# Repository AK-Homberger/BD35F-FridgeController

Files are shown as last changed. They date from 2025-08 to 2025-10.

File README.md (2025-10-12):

# BD35F Fridge Controller
An electronic thermostat for a Danfoss/Secop [BD35F](https://assets.danfoss.com/documents/latest/178661/AI376451289296en-000101.pdf) Compressor with ESP8266 (D1 Mini).

Secomp

The Danfoss/Secop BD35F compressor is a widely used DC powered compressor. I'm using it on my boat to cool the fridge. Unfortunately, the original thermostat was defect. Therfore, I decided to create an electronic alternative that has more features than the standard mechanical one.

## Features:
- Uses ESP8266 (D1 Mini) as processor.
- Dual language support (English/German).
- Easy upload of firmware without Arduino IDE possible.
- Temperature is measured with [DS18B20](https://encrypted-tbn0.gstatic.com/shopping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) sensor.
- Implements a Two-Point with I controller to increase the accuracy.
- Supports variable compressor speeds (2000 - 3500 RPM) to adjust cooling capacity and power consumption.
- Supports Boost function to cool down with more power.
- Supports automatic or manual Defrost routine.
- WLAN support (AP or client mode). Configurable via Wifi Manager.
- Browser interface and MDNS support (http://fridgecontrol.local).
- All parameters are configurable with a browser and stored in flash memory of ESP8266.
- [PCB](https://github.com/AK-Homberger/BD35F-FridgeController/blob/main/BD35F-FridgeController/BD35F-FridgeController-PCB.pdf) layout is available in repository (KiCad) and can be orderd from [Aisler.net](https://aisler.net/p/VBBOGMUR).

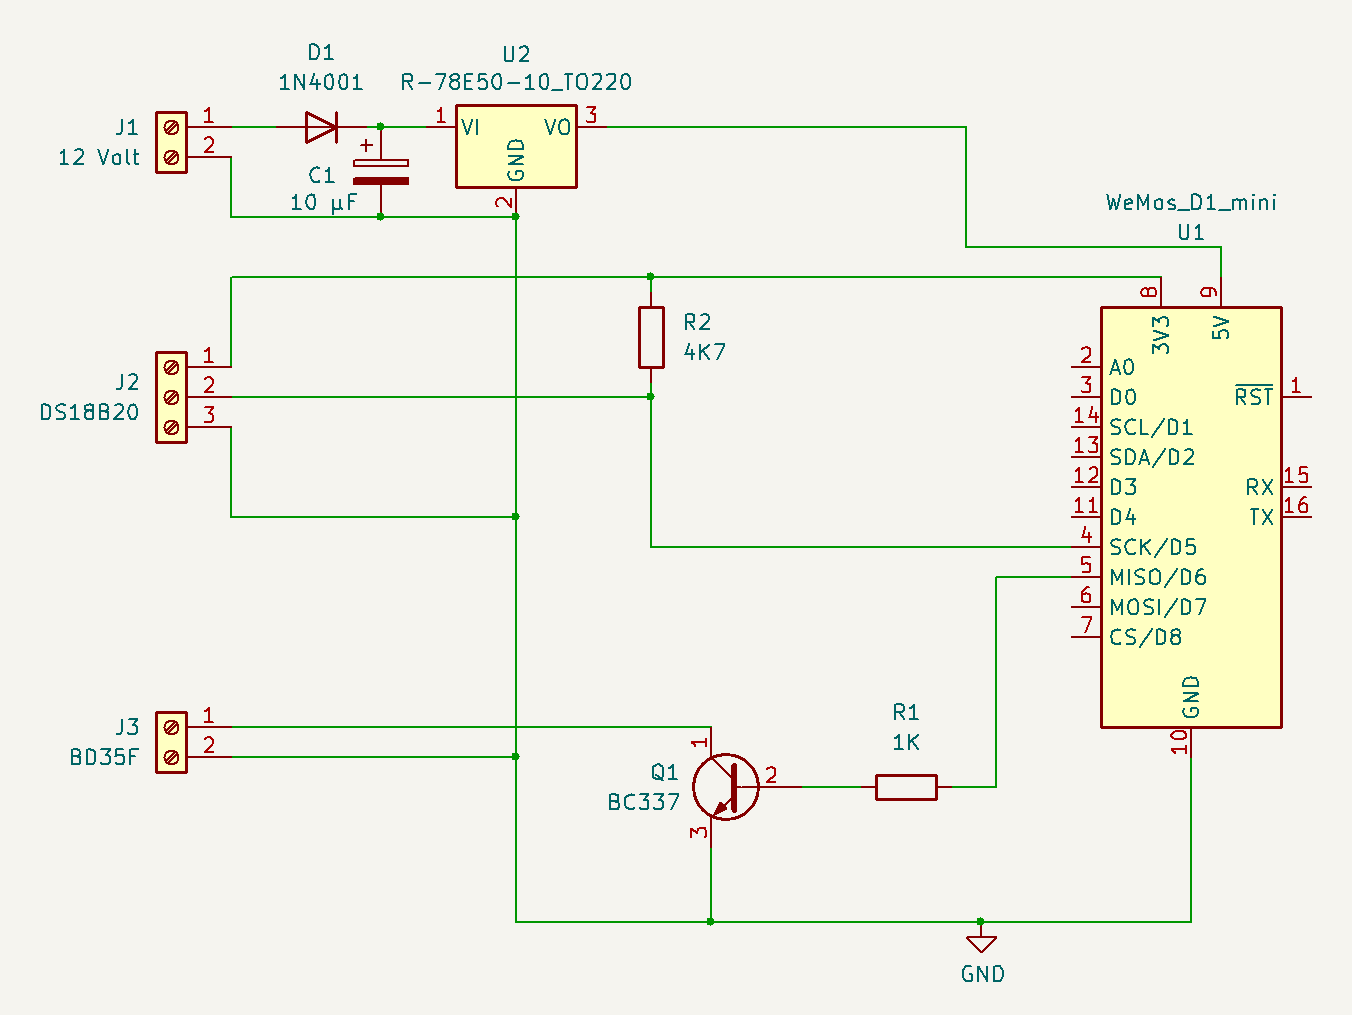
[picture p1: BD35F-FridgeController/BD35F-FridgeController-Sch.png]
Schematic


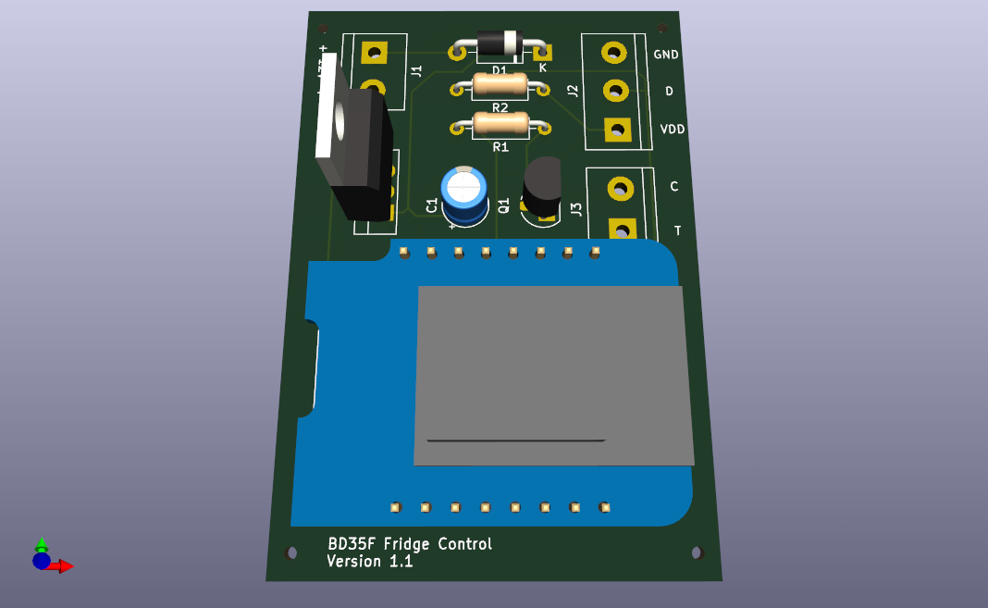
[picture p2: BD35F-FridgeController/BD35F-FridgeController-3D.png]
PCB


## Hardware
The hardware is based on an ESP8266 (D1 Mini) and a few additional parts. The 5 Volt supply voltage for the D1 Mini is created with a [step-down](https://www.reichelt.de/de/de/shop/produkt/dc_dc-wandler_r78e_5_v_500_ma_single-159161) converter. 
The temperature is measuered with a [DS18B20](https://www.analog.com/media/en/technical-documentation/data-sheets/ds18b20.pdf) sensor. The compressor is controlled with an open collector transistor between the connection T and C on the BD35F. 

The BD35F is measuering the current between T and C. C is on GND level and T has a pull-up resistor to 5 Volt. Only a few milliampere are flowing. A small NPN transitor (BC337) is sufficient here. There are two options: T permanently on GND level means 2000 RPM speed. A PWM signal (5 KHz) with a defined duty-cycle is used to set speeds from 2000 to 3500 RPM.

The PCB has three connectors:

### 1. Power 
Connect +/-to 12 Volt to the J1 connector. There is a protection against wrong cabling for +/-.

### 2. DS18B20 Temperature Sensor
Connect the three cables from the DS18B20 to the connector J2. The data line has already the pull-up resistor on the PCB. Red = VDD, Yello = D, Blue = GND.
Place the Sensor in the Fridge in middle highth.

### 3. BD35F Compressor
Connect J3 to the compressor connector. Remove the old thermostat cables and connect the cables C and  T to the compressor. You need appropriate cable shoes for the connection.

## Software
There are two ways to install the software to the D1 Mini. Either you install the Arduino IDE or you direcly flash the BIN-file to the device.

### Arduino IDE
Just [download](https://www.arduino.cc/en/software/) the IDE (version 2.x works well). Then add the Boad URL in preferences: "https://arduino.esp8266.com/stable/package_esp8266com_index.json" and install the Board software in the IDE. Then install the following libraries with the library manager:

- WiFiManager
- ArduinoJson
- OneWire
- DallasTemperature
- Preferences

Then download the sketch from GitHud (Button "Code" and download as ZIP) and extract it. Then move to the [FridgeControl.ino](https://github.com/AK-Homberger/BD35F-FridgeController/blob/main/FridgeControl/FridgeControl.ino) file and open the sketch.
Connect the D1 mini with an USB-Cable to the PC and upload the sketch to the D1 Mini. Later uploads can be done with the OTA function via network.

### NodeMCU-PyFlasher
This works without installation of the IDE. Simply download the [NodeMCU-PyFlasher](https://github.com/nodemcu/nodemcu-firmware/releases) and start it. 

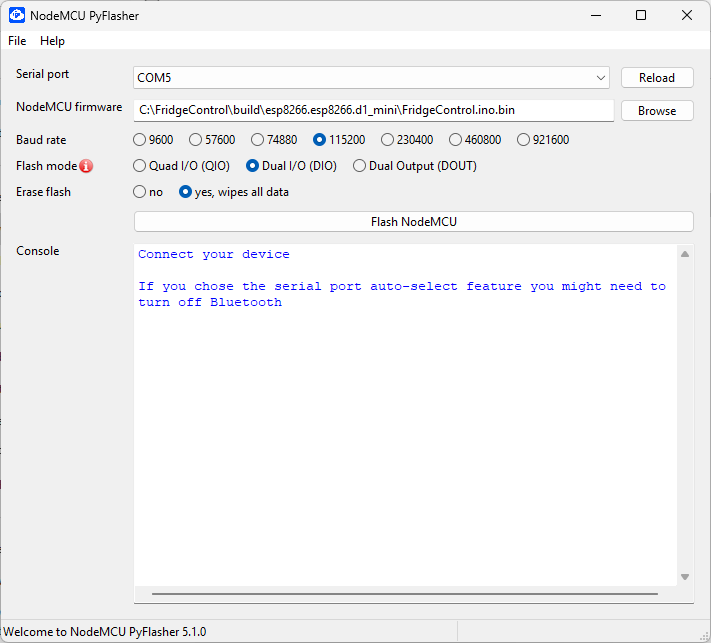
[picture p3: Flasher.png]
Flasher


Select appropriate serial port and then move to the bin file in the deownloaded code. Use the seetings as shown for the upload.

## Usage

After upload of the firmware you have to re-power the device to start the [Wifi-Manager](https://github.com/tzapu/WiFiManager) (within 2 minutes after restart). Just look for a new WLAN network with the name "Fridgeconfig_AP" and connect to it, without a password. The browser will start automatically. Then select the network (ssid) you want to connect to and enter the password. 

If you don't configure or press "Exit" the device remain in AP mode with a changed name "Fridgecontrol_AP".

You can use this to test the device without a real network to connect to. But this is an open connection. Don't use this permanently.

To start the web interface enter "http://fridgecontrol.local" in the browser. The interface looks then like this:

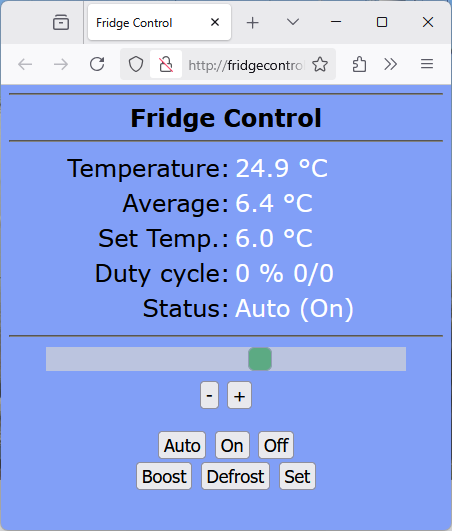
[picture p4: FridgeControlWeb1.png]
Web1


The page shows the current fridge temperature, the average temperature, the desired set temperature. Duty cycle shows the percentage of the on time compared to the last on and off time cycle. The values are also shown in minutes (On/Off). The status filed shows the staus of the controller (Auto, On, Off, Boost or Defrost).

With the slidebar and +/- you can modify the the set temperature.

With the buttons you can set the mode:

- Auto: Standard mode to control the temperature.
- ON: Switch on the compressor permanently.
- Off: Switch off the compressor permanently.
- Boost: Cool down for a defined time with a different set point, hysteresis and speed.
- Defrost: Manually start a defrost cycle.
- Set: Opens a settings page.

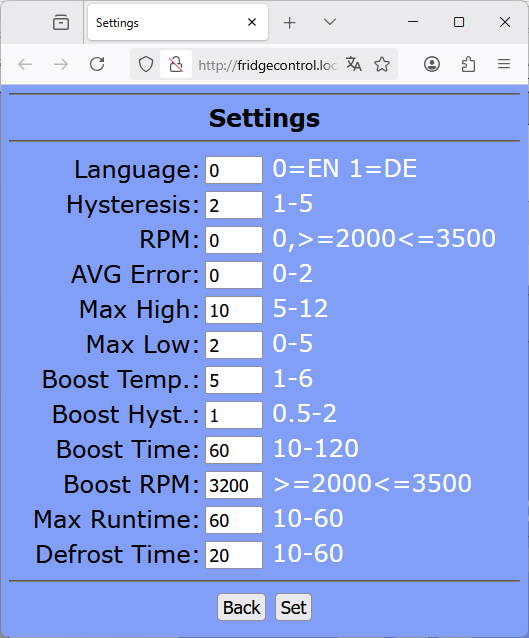
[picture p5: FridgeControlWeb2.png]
Web2


With the settings page you can control the behaviour of the controller without a need to recompile the code. The following settings are available:

- Language:   0=English 1=German language
- Hysteresis: Sets the Hysteresis/deviation for the two point controller. 2 means +/- 2 K. For a set temperature of 6 that means the temperature will between 4 and 8 degrees.
- RPM:         The desired speed of the compressor. Set as low as possible to reduce power consumption (2000 = 3,5A, 3500 = 7A). "0" means T permanently to GND and 2000 RPM (original mechanical thermostat behaviour).
- AVG Error:   This is the allowed deviation from the average. 0 means the compressor will cool down in every cycle until the average temperature reaches the set temperature. The average temperature is calculated with a low pass filter with K of 1/3600. Means average over about one hour.
- Max          High: The maximum high temperture. The compressor will be switched off, if ths level is reached. Independent of average temperature.
- Max Low:     The maximum low temperture. The compressor will be switched on, if ths level is reached. Independent of average temperature.
- Boost Temp.: Desired temperature for the boost function.
- Boost Hyst.: Hysteresis/deviation for the boost function.
- Boost Time   Time in minutes for the boost function.
- Boost RPM:   Compressor speed for the boost function.
- Max Runtime: Used to detect a needed defrost cycle. If the compressor runs for the defined time, a mandatory defrost cycle will start.
- Defrost Time: Set the time for the defrost cycle. Time depends on local fridge details.

After changes press the "Set" butten. The entered value will be checked against the allowed ranges. If everyting is OK you can use "Back" to go back to the main page.

# Parts
- PCB [Aisler](https://aisler.net/p/VBBOGMUR)
- U1 D1 Mini [Link](https://www.reichelt.de/de/en/d1-mini-esp8266-v3-0-d1-mini-p253978.html?&nbc=1)
- U2 Voltage regulator [Link](https://www.reichelt.de/de/de/shop/produkt/dc_dc-wandler_r78e_5_v_500_ma_single-159161)
- R1 Resistor 1 KOhm [Link](https://www.reichelt.de/de/en/carbon-film-resistor-1-4-w-5-1-0-kilo-ohms-1-4w-1-0k-p1315.html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)
- R2 Resistor 4,7 KOhm [Link](https://www.reichelt.com/de/en/shop/product/carbon_film_resistor_1_4_w_5_4_7_kohm-1425)
- Q1 Transistor BC337 [Link](https://www.reichelt.de/de/en/transistor-to-92-bl-npn-45v-800ma-bc-337-25-dio-p219125.html?&nbc=1)
- D1 Diode 1N4001 [Link](https://www.reichelt.de/de/en/rectifier-diode-do41-50-v-1-a-1n-4001-p1723.html?&nbc=1)
- C1 Condensator 10µF [Link](https://www.reichelt.de/de/de/shop/produkt/tantal-kondensator_10_f_10_35v_rm_2_5-20334)
- J1/J3 Connector 2-pin (*2) [Link](https://www.reichelt.de/de/en/2-pin-terminal-strip-spacing-5-08-akl-101-02-p36605.html?&nbc=1)
- J2 Connector 3-pin [Link](https://www.reichelt.com/de/en/shop/product/3-pin_terminal_strip_spacing_5_08-36606)
- DS18B20 [Link](https://www.reichelt.com/de/en/shop/product/shelly_temperature_sensor_ds18b20-287127)

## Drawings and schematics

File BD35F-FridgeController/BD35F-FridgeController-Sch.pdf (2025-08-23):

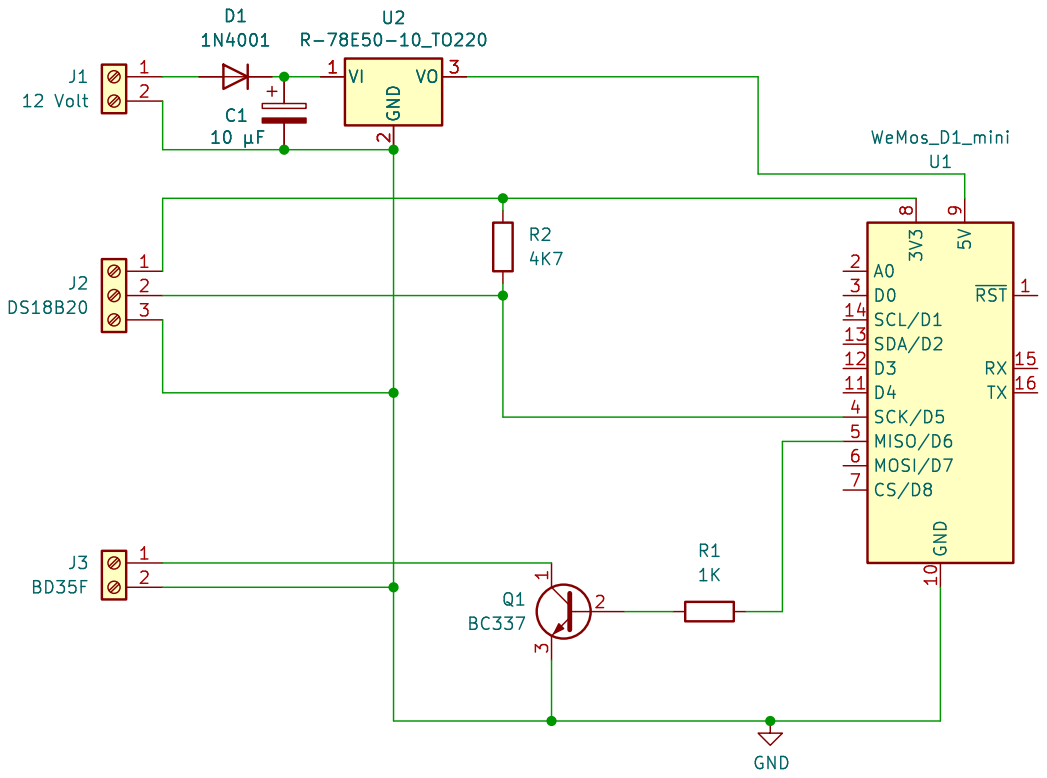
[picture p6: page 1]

2 VO 3 U2 R-78E50-10_TO220 ~{RST}1 GND 10 D4 11 D3 12 SDA/D2 13 SCL/D1 14 RX 15 TX 16 A0 2 D0 3 SCK/D5 4 MISO/D6 5 MOSI/D7 6 CS/D8 7 3V3

Id: 1/1 Title: File: BD35F-FridgeController.kicad_sch Sheet: /

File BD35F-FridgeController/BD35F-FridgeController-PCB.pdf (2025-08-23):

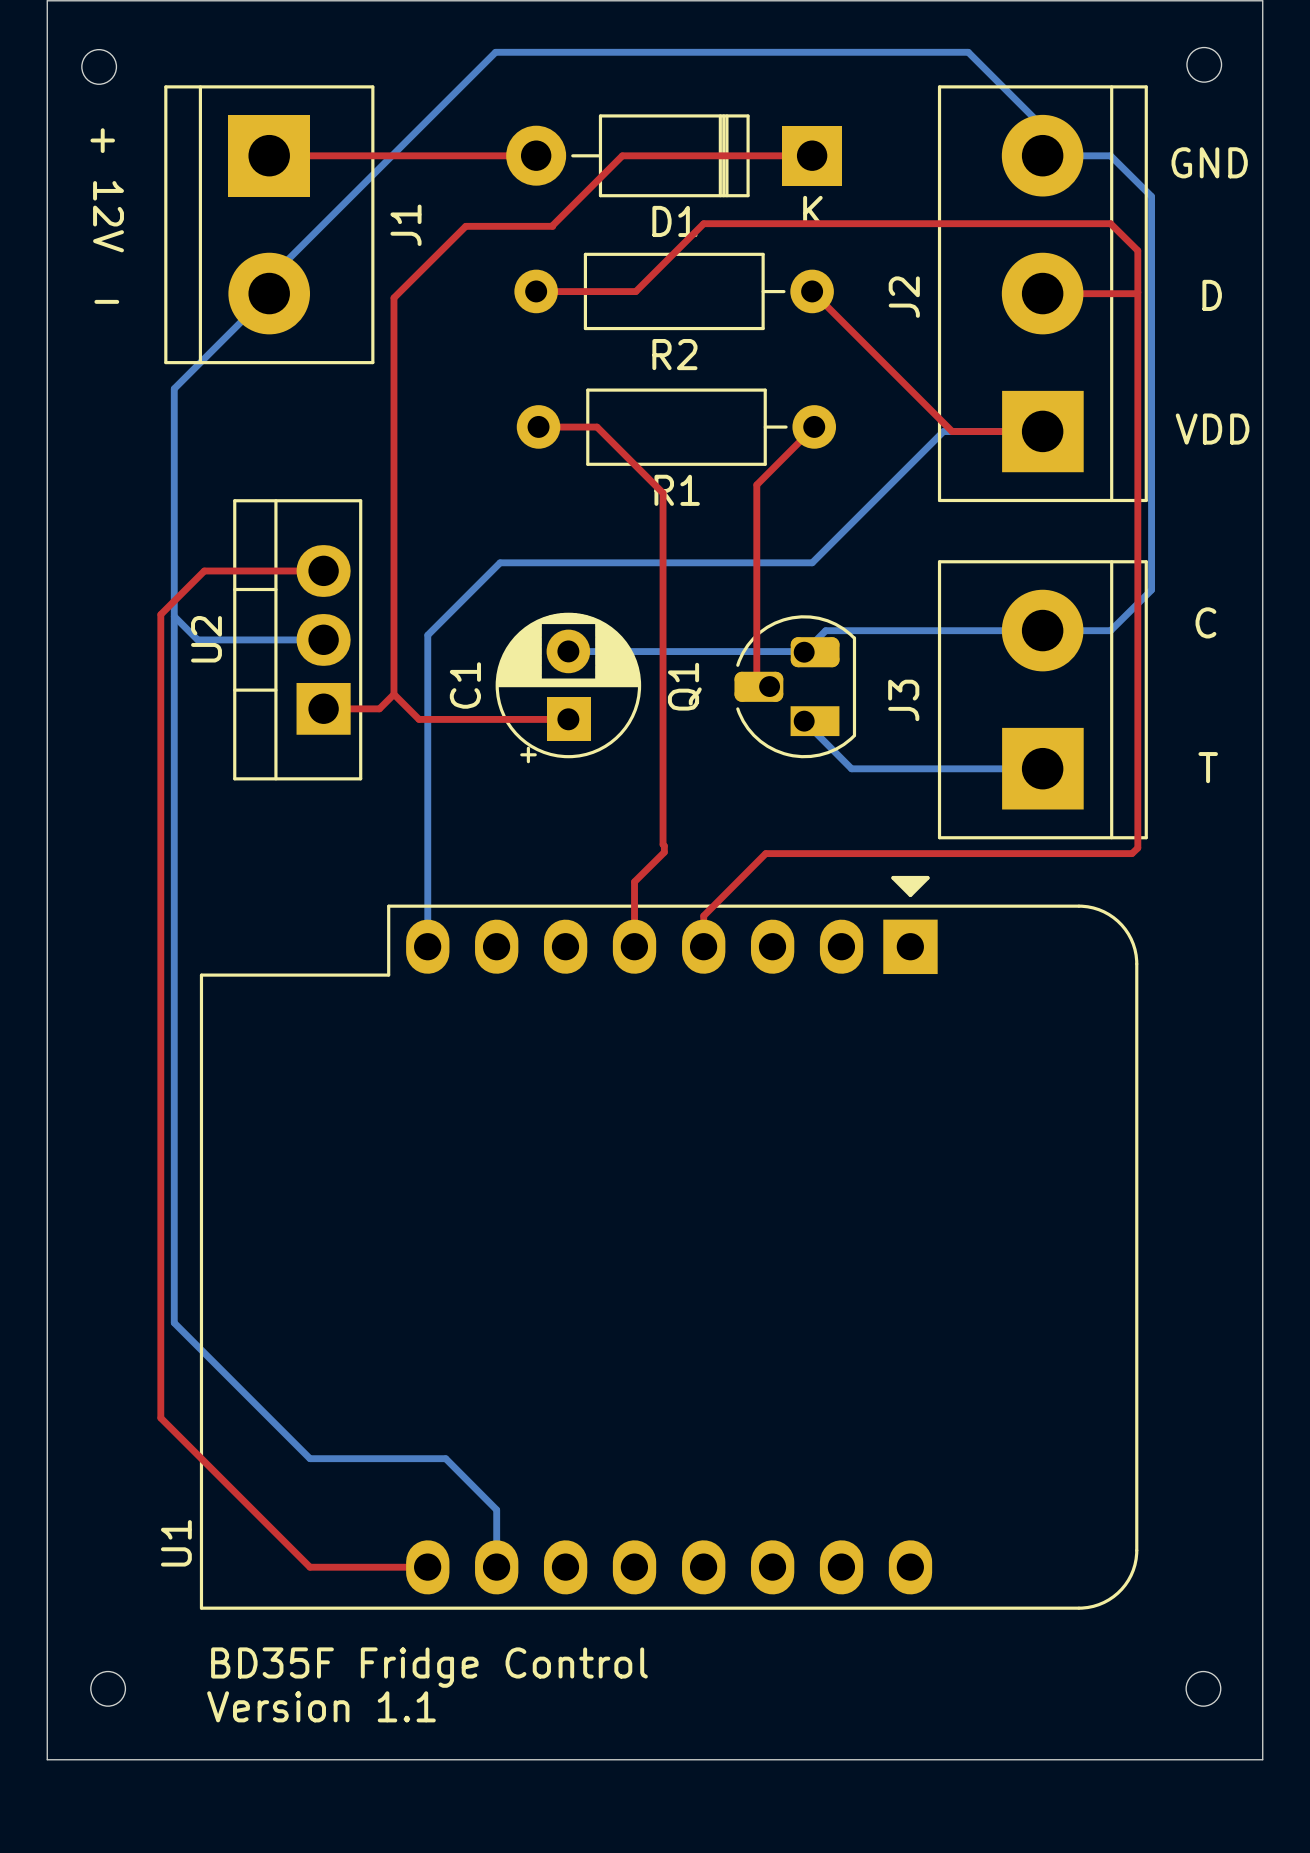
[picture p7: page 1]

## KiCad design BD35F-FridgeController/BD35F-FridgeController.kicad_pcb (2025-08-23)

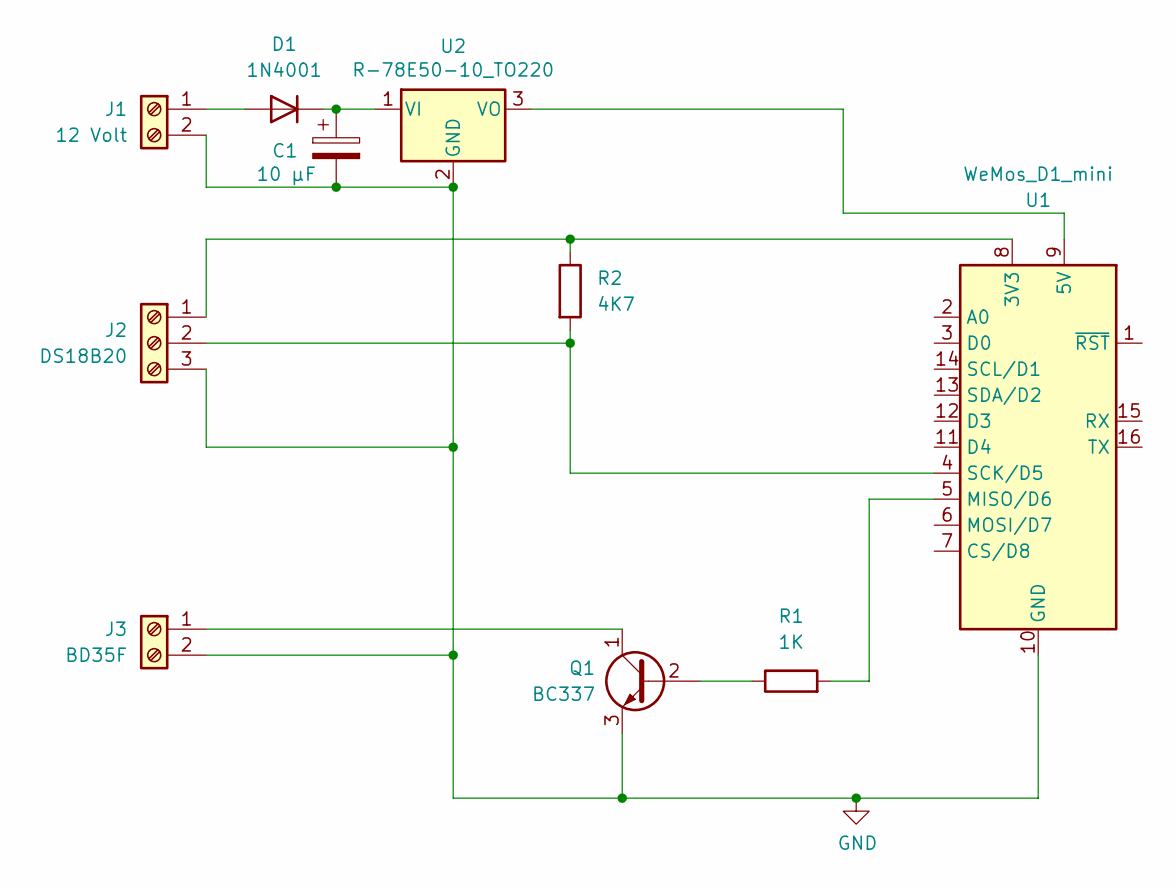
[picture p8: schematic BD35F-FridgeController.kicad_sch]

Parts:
C1: 10 µF; CP_Radial_D5.0mm_P2.50mm
D1: 1N4001; D_DO-41_SOD81_P10.16mm_Horizontal
J1: 12 Volt; TerminalBlock_bornier-2_P5.08mm
J2: DS18B20; TerminalBlock_bornier-3_P5.08mm
J3: BD35F; TerminalBlock_bornier-2_P5.08mm
Q1: BC337; TO-92_HandSolder
R1: 1K; R_Axial_DIN0207_L6.3mm_D2.5mm_P10.16mm_Horizontal
R2: 4K7; R_Axial_DIN0207_L6.3mm_D2.5mm_P10.16mm_Horizontal
U1: WeMos_D1_mini; WEMOS_D1_mini_light
U2: R-78E50-10_TO220; TO-220-3_Vertical

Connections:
GND: C1.2, J1.2, J2.3, J3.2, Q1.3 (E), U1.10 (GND), U2.2 (GND)
unnamed: D1.2 (A), J1.1
unnamed: C1.1, D1.1 (K), U2.1 (VI)
unnamed: J2.1, R2.1, U1.8 (3V3)
unnamed: J2.2, R2.2, U1.4 (SCK/D5)
unnamed: J3.1, Q1.1 (C)
unnamed: Q1.2 (B), R1.1
unnamed: U1.9 (5V), U2.3 (VO)
unnamed: R1.2, U1.5 (MISO/D6)

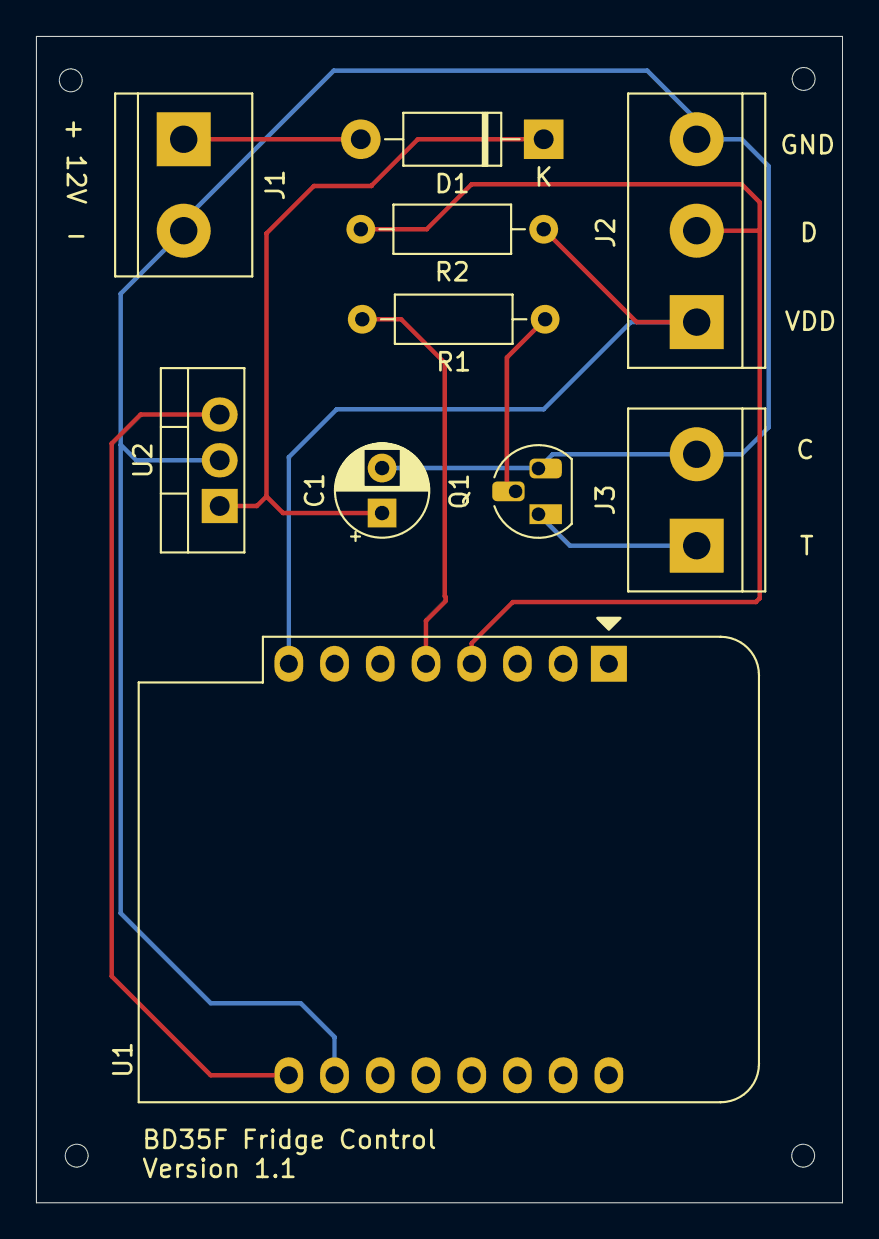
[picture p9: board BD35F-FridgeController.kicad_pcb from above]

Board: 2 copper layers, 44.8 x 64.8 mm, 10 parts (0 on the bottom side), 9 nets.

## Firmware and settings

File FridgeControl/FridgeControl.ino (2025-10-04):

/*
  This code is free software; you can redistribute it and/or
  modify it under the terms of the GNU Lesser General Public
  License as published by the Free Software Foundation; either
  version 2.1 of the License, or (at your option) any later version.
  This code is distributed in the hope that it will be useful,
  but WITHOUT ANY WARRANTY; without even the implied warranty of
  MERCHANTABILITY or FITNESS FOR A PARTICULAR PURPOSE.  See the GNU
  Lesser General Public License for more details.
  You should have received a copy of the GNU Lesser General Public
  License along with this library; if not, write to the Free Software
  Foundation, Inc., 51 Franklin St, Fifth Floor, Boston, MA  02110-1301  USA
*/

// Fridge Control for Danfoss/Secomp BD35F with WLAN and compressor speed setting
// Implements Two-Point with I controller to improve precision of temperature control

// DS18B20 temperature sensor on D5 pin, Relay / PWM output on pin D6
// Use 4k7 Ohm resitor as Pull-Up on D5 (to 3,3 Volt)
// Supports relay output (On/Off) or PWM with NPN transistor to control compressor speed between 2000 and 3500 RPM
// Set PWM to 0 for relay mode
// Connect Relay output (NO) or NPN Transitor (Open Collector) between T and C connection (C = GND, T at 5 Volt level with resistor)
// Current between T and C is only a few mA. A small transistor (eg. BC337) is sufficient. Use 1 kOhm between output pin and basis.

// Version 1.1, 04.10.2025, AK-Homberger
// Corrected duty cycle calculation (double type)

#include <ESP8266WiFi.h>
#include <ESP8266WebServer.h>
#include <ArduinoOTA.h>

// External libraries. Install via Library Manager in IDE
#include <WiFiManager.h>    // https://github.com/tzapu/WiFiManager
#include <ArduinoJson.h>
#include <OneWire.h>
#include <DallasTemperature.h>
#include <Preferences.h>

// Local include
#include "fridge_html_de.h"  // HTML and Javascript code German
#include "fridge_html_en.h"  // HTML and Javascript code English

#define On true
#define Off false

// GPIOs
const int SensorPin = D5;  // DS1820 Sensor
const int FridgePin = D6;  // Relay pin or PWM pin with NPN Transistor

// Put IP address details here
IPAddress AP_local_ip(192, 168, 4, 1);  // Static address for AP
IPAddress AP_gateway(192, 168, 4, 1);
IPAddress AP_subnet(255, 255, 255, 0);

// Fridge
unsigned Language = 0;                  // Language 0=English 1=German
unsigned CurrentRPM = 0;                // Initial RPM. Current value is stored in NVS. 0 = Relay mode
double FridgeTemp = -100;               // Measured fridge temperature
double FridgeTempAvg = -100;            // Average temperature over about one hour (low pass filter)
double FridgeTempLevel = 6;             // Initial temperature level. Current value is stored in NVS
double FridgeHyst = 2;                  // Hysteresis / 2. Max deviation from set temperaure level
double FridgeMaxHigh = 10;              // Maximum temperature. Compressor will switch on above this temperature
double FridgeMaxLow = 2;                // Minimum temperature. Compressor will switch off below this temperature
double FridgeAvgError = 0.1;            // Maximum allowed deviation from average temperatur (forms I part of the control)
bool FridgeAuto = true;                 // Fridge in automatic mode
bool FridgeBoost = false;               // Fridge in boost mode
bool FridgeDefrost = false;             // Fridge in defrost mode
unsigned FridgeDefrostTime = 20;        // Defrost time
unsigned FridgeCurrentDefrostTime = 0;  // Current defrost time
unsigned FridgeMaxRuntime = 60;         // Maximum runtime for compresser. Then defrost
unsigned FridgeCurrentBoostTime = 0;    // Current boost time (counts up to boost time)
double FridgeBoostTemp = 5;             // Fridge boost temperatur (with fixed hysteresis/deviation of 1 K)
double FridgeBoostHyst = 1;             // Set hsyteresis for boost
unsigned FridgeBoostTime = 60;          // Set boost time
unsigned FridgeBoostRPM = 3000;         // Set boost speed for compressor
unsigned FridgeOnTime = 0;              // Current on time of compressor. Counts up.
unsigned FridgeOffTime = 0;             // Current off time of compressor. Counts up.
unsigned FridgeLastOnTime = 0;          // Last on time of compressor to calculate duty cycle
unsigned FridgeLastOffTime = 0;         // Last off time of compressor to calculate duty cycle
bool FridgeOnOff = Off;                 // Current compessor state
bool f_update = false;                  // NVS values changed. Store new values.

// Web Server
ESP8266WebServer web_server(80);  // Web Server at port 80

// Setup a oneWire instance to communicate with any OneWire devices (not just Maxim/Dallas temperature ICs)
OneWire oneWire(SensorPin);
// Pass our oneWire reference to Dallas Temperature.
DallasTemperature sensors(&oneWire);

// Nonvolatile storage on ESP
Preferences preferences;

//*****************************************************************************
void setup() {
  // Sensor and Thermostat pin
  //pinMode(SensorPin, INPUT_PULLUP);  // Comment out if you use an external pull up resistor
  pinMode(FridgePin, OUTPUT);        // Sets relay/PWM pin as output
  analogWriteFreq(5000);             // BD35F expects 5 kHz for PWM with duty cycle control

  // Init serial
  Serial.begin(115200);
  Serial.println();

  WiFiManager wm;
  wm.setConfigPortalTimeout(120);
  
  // Set HTTP request events
  web_server.on("/", HandleRoot);                       // This is the Main display page
  web_server.on("/f_temp", GetFridgeData);              // To get fridge temperature and states
  web_server.on("/f_up", FridgeUp);                     // Fridge + 0.1
  web_server.on("/f_down", FridgeDown);                 // Fridge - 0.1
  web_server.on("/f_auto", Fridge_Auto);                // Fridge Auto state
  web_server.on("/f_boost", Fridge_Boost);              // Fridge Boost state
  web_server.on("/f_defrost", Fridge_Defrost);          // Fridge Defrost state
  web_server.on("/f_on", FridgeOn);                     // Switch fridge On
  web_server.on("/f_off", FridgeOff);                   // Switch fridge Off
  web_server.on("/f_slider", FridgeSlider);             // Handle fridge slider move
  web_server.on("/f_settings", handleSettings);         // Settings page
  web_server.on("/f_get_settings", handleGetSettings);  // JS get settings
  web_server.on("/f_set_settings", handleSetSettings);  // JS save settings

  web_server.onNotFound(HandleNotFound);

  if (!wm.autoConnect("Fridgeconfig_AP")) {
    Serial.println("Start AP");
    WiFi.mode(WIFI_OFF);
    delay(100);
    WiFi.mode(WIFI_AP);
    WiFi.softAP("Fridgecontrol_AP");
    IPAddress IP = WiFi.softAPIP();
    Serial.print("AP IP address: ");
    Serial.println(IP);    
  }

  // Start OneWire
  sensors.begin();
  sensors.setWaitForConversion(false);  // Set to asynchronus mode
  sensors.requestTemperatures();        // Initial request right now

  // Start web server
  web_server.begin();
  Serial.println("HTTP Server started");

  // Start OTA
  ArduinoOTA.setHostname("FridgeControl");  // Arduino OTA config and start
  ArduinoOTA.begin(true);                   // With MDNS (open with http://fridgecontrol.local)

  // Read stored data
  preferences.begin("nvs", false);  // Open nonvolatile storage (nvs)
  Language = preferences.getInt("Language", 0);
  FridgeTempLevel = preferences.getFloat("FridgeTempLevel", 6);
  FridgeHyst = preferences.getFloat("FridgeHyst", 2);
  FridgeMaxHigh = preferences.getFloat("FridgeMaxHigh", 10);
  FridgeMaxLow = preferences.getFloat("FridgeMaxLow", 2);
  FridgeAvgError = preferences.getFloat("FridgeAvgError", 0);
  CurrentRPM = preferences.getInt("RPM", 0);
  FridgeBoostTime = preferences.getInt("FridgeBoostTime", 60);
  FridgeBoostTemp = preferences.getFloat("FridgeBoostTemp", 5);
  FridgeBoostHyst = preferences.getFloat("FridgeBoostHyst", 1);
  FridgeBoostRPM = preferences.getInt("FridgeBoostRPM", 3200);
  FridgeMaxRuntime = preferences.getInt("FridgeMaxRuntime", 60);
  FridgeDefrostTime = preferences.getInt("FridgeDefrostTime", 20);
  preferences.end();
}


//****************************************************************************************
// Read DS1820 sensor once per second (non blocking mode)

void GetTemperature() {
  static float FTO = 0;
  static unsigned long LastTime = 0;
  double tmp = 0;

  if (millis() - LastTime > 1000) {
    tmp = sensors.getTempCByIndex(0);
    //Serial.println(tmp);
    if (tmp != -127) {
      if (abs(FTO - tmp) < 1) FridgeTemp = tmp;
      FTO = tmp;
    }
    LastTime = millis();
    sensors.requestTemperatures();  // Send the command to get temperatures
  }
}


//****************************************************************************************
void HandleRoot() {
  if (Language == 0) web_server.send(200, "text/html", FRIDGE_page_en);  //Send web page
  if (Language == 1) web_server.send(200, "text/html", FRIDGE_page_de);  //Send web page
}


//****************************************************************************************
void handleSettings() {
  if (Language == 0) web_server.send(200, "text/html", Settings_page_en);  //Send settings web page
  if (Language == 1) web_server.send(200, "text/html", Settings_page_de);  //Send settings web page
}


//****************************************************************************************
void handleGetSettings() {
  String Text;
  JsonDocument root;

  root["hyst"] = FridgeHyst;
  root["level"] = FridgeTempLevel;
  root["rpm"] = CurrentRPM;
  root["avgerror"] = FridgeAvgError;
  root["maxhigh"] = FridgeMaxHigh;
  root["maxlow"] = FridgeMaxLow;
  root["boosttime"] = FridgeBoostTime;
  root["boosttemp"] = FridgeBoostTemp;
  root["boosthyst"] = FridgeBoostHyst;
  root["boostrpm"] = FridgeBoostRPM;
  root["maxruntime"] = FridgeMaxRuntime;
  root["defrosttime"] = FridgeDefrostTime;
  root["language"] = Language;

  serializeJsonPretty(root, Text);
  web_server.send(200, "text/plain", Text);  //Send values to client ajax request
}


//****************************************************************************************
void handleSetSettings() {
  float tmp;

  if (web_server.args() == 12) {

    tmp = web_server.arg(0).toFloat();
    if (tmp >= 1 && tmp <= 5) FridgeHyst = tmp;

    tmp = web_server.arg(1).toInt();
    if ((tmp == 0) || (tmp >= 2000 && tmp <= 3500)) CurrentRPM = tmp;  // 0 = Relay mode

    tmp = web_server.arg(2).toFloat();
    if (tmp >= 0 && tmp <= 2) FridgeAvgError = tmp;

    tmp = web_server.arg(3).toFloat();
    if (tmp >= 0 && tmp <= 5) FridgeMaxLow = tmp;

    tmp = web_server.arg(4).toFloat();
    if (tmp >= 5 && tmp <= 12) FridgeMaxHigh = tmp;

    tmp = web_server.arg(5).toInt();
    if (tmp >= 10 && tmp <= 120) FridgeBoostTime = tmp;

    tmp = web_server.arg(6).toInt();
    if (tmp >= 2000 && tmp <= 3500) FridgeBoostRPM = tmp;

    tmp = web_server.arg(7).toFloat();
    if (tmp >= 1 && tmp <= 6) FridgeBoostTemp = tmp;

    tmp = web_server.arg(8).toInt();
    if (tmp >= 10 && tmp <= 60) FridgeMaxRuntime = tmp;

    tmp = web_server.arg(9).toInt();
    if (tmp >= 10 && tmp <= 60) FridgeDefrostTime = tmp;

    tmp = web_server.arg(10).toFloat();
    if (tmp >= 0.5 && tmp <= 2) FridgeBoostHyst = tmp;

    tmp = web_server.arg(11).toInt();
    if (tmp >= 0 && tmp <= 1) Language = tmp;

    web_server.send(200, "text/html");
    f_update = true;
  }
}


//****************************************************************************************
// Handle UP button

void FridgeUp() {
  FridgeTempLevel += 0.1;
  if (FridgeTempLevel > 10) FridgeTempLevel = 10;
  f_update = true;
  web_server.send(200);
}


//****************************************************************************************
// Handle Down button

void FridgeDown() {
  FridgeTempLevel -= 0.1;
  if (FridgeTempLevel < 0) FridgeTempLevel = 0;
  f_update = true;
  web_server.send(200);
}


//****************************************************************************************
// Handle Auto button

void Fridge_Auto() {
  FridgeAuto = true;
  FridgeBoost = false;
  FridgeDefrost = false;
  web_server.send(200);
}


//****************************************************************************************
// Handle Boost button

void Fridge_Boost() {

  FridgeBoost = true;
  FridgeAuto = false;
  FridgeDefrost = false;
  FridgeCurrentBoostTime = 0;

  if (FridgeOnOff == On) {
    FridgeSwitch(Off);
    delay(500);
    FridgeSwitch(On);
  }
  web_server.send(200);
}


//****************************************************************************************
// Handle Defrost button

void Fridge_Defrost() {

  FridgeDefrost = true;
  FridgeAuto = false;
  FridgeBoost = false;
  FridgeCurrentDefrostTime = 0;
  FridgeSwitch(Off);
  web_server.send(200);
}


//****************************************************************************************
// Handle On button

void FridgeOn() {
  FridgeSwitch(On);
  FridgeAuto = false;
  FridgeBoost = false;
  FridgeDefrost = false;
  web_server.send(200);
}


//****************************************************************************************
// Handle Off button

void FridgeOff() {
  FridgeSwitch(Off);
  FridgeAuto = false;
  FridgeBoost = false;
  FridgeDefrost = false;
  web_server.send(200);
}


//****************************************************************************************
// Handle slider event

void FridgeSlider() {
  if (web_server.args() > 0) {
    FridgeTempLevel = web_server.arg(0).toFloat();
  }
  f_update = true;
  web_server.send(200);
}


//****************************************************************************************
// Send temperature, level and status as JSON string

void GetFridgeData() {
  String Text, State;
  char buf[30];
  double dutyCycle = 0;
  JsonDocument root;

  if (FridgeDefrost == true) {
    snprintf(buf, sizeof(buf), "Defrost (%d)", FridgeDefrostTime - (FridgeCurrentDefrostTime / 60));
    State = buf;
  } else if (FridgeBoost == true) {
    if (FridgeOnOff == On) {
      snprintf(buf, sizeof(buf), "Boost (%d)", FridgeBoostTime - (FridgeCurrentBoostTime / 60));
      State = buf;
    }
    if (FridgeOnOff == Off) {
      snprintf(buf, sizeof(buf), "Boost (%d)", FridgeBoostTime - (FridgeCurrentBoostTime / 60));
      State = buf;
    }
  } else if (FridgeAuto) {
    if (Language == 0 && FridgeOnOff == On) State = "Auto (On)";
    if (Language == 1 && FridgeOnOff == On) State = "Auto (An)";
    if (Language == 0 && FridgeOnOff == Off) State = "Auto (Off)";
    if (Language == 1 && FridgeOnOff == Off) State = "Auto (Aus)";
  } else {
    if (Language == 0 && FridgeOnOff) State = "On";
    if (Language == 1 && FridgeOnOff) State = "An";
    if (Language == 0 && !FridgeOnOff) State = "Off";
    if (Language == 1 && !FridgeOnOff) State = "Aus";
  }

  root["status"] = State;

  snprintf(buf, sizeof(buf), "%4.1f", FridgeTemp);
  root["temp"] = buf;

  snprintf(buf, sizeof(buf), "%4.1f", FridgeTempLevel);
  root["level"] = buf;

  snprintf(buf, sizeof(buf), "%4.1f", FridgeTempAvg);
  root["avg"] = buf;

  if ((FridgeLastOffTime + FridgeLastOnTime) != 0) {
    dutyCycle = (double)FridgeLastOnTime / ((double)FridgeLastOnTime + (double)FridgeLastOffTime) * 100.0;
  }

  snprintf(buf, sizeof(buf), "%3.0f %% %1.0f/%1.0f", dutyCycle, FridgeLastOnTime / 60.0, FridgeLastOffTime / 60.0);
  root["dutycycle"] = buf;

  serializeJsonPretty(root, Text);
  web_server.send(200, "text/plain", Text);  //Send sensors values to client ajax request
}


//****************************************************************************************
void HandleNotFound() {  // Unknown request. Send error 404
  web_server.send(404, "text/plain", "File Not Found\n\n");
}


//****************************************************************************************
// Handle Fridge

void HandleFridgeControl() {
  static unsigned long LastTime = 0;

  if (millis() - LastTime > 1000) {

    if ((FridgeOnTime > FridgeMaxRuntime * 60) && FridgeDefrost == false) {  // Compressor runs more than an hour -> Defrost
      FridgeSwitch(Off);
      FridgeDefrost = true;
      FridgeCurrentDefrostTime = 0;
    }

    if (FridgeOnOff == On) {
      FridgeOnTime++;
    } else {
      FridgeOffTime++;
    }

    // Set initial average temperature after start to set temperature level when first temperature measuered
    if (FridgeTempAvg == -100 && FridgeTemp != -100) FridgeTempAvg = FridgeTempLevel;

    // Calculate average temperature with low pass filter (K = 1/3600). Means average over about one hour.
    FridgeTempAvg = FridgeTempAvg + ((FridgeTemp - FridgeTempAvg) / 3600.0);

    if (f_update) {  // Store values if changed
      preferences.begin("nvs", false);
      preferences.putInt("Language", Language);
      preferences.putFloat("FridgeTempLevel", FridgeTempLevel);
      preferences.putFloat("FridgeHyst", FridgeHyst);
      preferences.putFloat("FridgeMaxHigh", FridgeMaxHigh);
      preferences.putFloat("FridgeMaxLow", FridgeMaxLow);
      preferences.putFloat("FridgeAvgError", FridgeAvgError);
      preferences.putInt("RPM", CurrentRPM);
      preferences.putFloat("FridgeBoostTemp", FridgeBoostTemp);
      preferences.putFloat("FridgeBoostHyst", FridgeBoostHyst);
      preferences.putInt("FridgeBoostTime", FridgeBoostTime);
      preferences.putInt("FridgeBoostRPM", FridgeBoostRPM);
      preferences.putInt("FridgeMaxRuntime", FridgeMaxRuntime);
      preferences.putInt("FridgeDefrostTime", FridgeDefrostTime);
      preferences.end();
      f_update = false;
    }

    if (FridgeDefrost == true) {  // Defrost for  FridgeDefrostTime in minutes
      FridgeCurrentDefrostTime++;
      if (FridgeCurrentDefrostTime > FridgeDefrostTime * 60) {
        FridgeDefrost = false;
        FridgeBoost = false;
        FridgeAuto = true;
        FridgeOnTime = 0;
        FridgeOffTime = 0;
      }
    } else if (FridgeBoost == true) {  // Switch On/Off depending on temperature for boost
      FridgeCurrentBoostTime++;

      if (FridgeTemp >= FridgeBoostTemp + FridgeBoostHyst) FridgeSwitch(On);
      if (FridgeTemp <= FridgeBoostTemp - FridgeBoostHyst) FridgeSwitch(Off);

      if (FridgeCurrentBoostTime > FridgeBoostTime * 60) {
        FridgeBoost = false;
        FridgeDefrost = false;
        FridgeAuto = true;
        FridgeOnTime = 0;
        FridgeOffTime = 0;
      }
    } else if (FridgeAuto == true) {  // Switch On/Off depending on temperatures

      if (((FridgeTemp <= FridgeTempLevel - FridgeHyst) && (FridgeTempAvg <= FridgeTempLevel + FridgeAvgError)) || (FridgeTemp <= FridgeMaxLow)) {
        FridgeSwitch(Off);
      }
      if (((FridgeTemp >= FridgeTempLevel + FridgeHyst) && (FridgeTempAvg >= FridgeTempLevel - FridgeAvgError)) || (FridgeTemp >= FridgeMaxHigh)) {
        FridgeSwitch(On);
      }
    }
    LastTime = millis();
  }
}


//****************************************************************************************
// Handle Fridge On/Off and duty cycle calculation

void FridgeSwitch(bool state) {
  unsigned DutyCycle = 0, RPM = 0;
  const unsigned MinDutyCycle = 220;  // 2000 RPM
  const unsigned MaxDutyCycle = 90;   // 3500 RPM

  FridgeOnOff = state;

  RPM = CurrentRPM;
  if (FridgeBoost == true) RPM = FridgeBoostRPM;

  if (RPM >= 2000) {
    DutyCycle = map(RPM, 2000, 3500, MinDutyCycle, MaxDutyCycle);
  } else {
    DutyCycle = 255;  // Relay mode. Duty cycle 255 = permanently On
  }

  if (state == On) {
    analogWrite(FridgePin, DutyCycle);  // On with duty cycle for RPM or permanently for relay
  } else {
    analogWrite(FridgePin, 0);  // Off
  }

  // Measure On/Off times for fridge duty cycle
  if (state == Off && FridgeOnTime != 0) {
    FridgeLastOnTime = FridgeOnTime;
    FridgeOnTime = 0;
  }

  if (state == On && FridgeOffTime != 0) {
    FridgeLastOffTime = FridgeOffTime;
    FridgeOffTime = 0;
  }
}


//*****************************************************************************
void loop() {
  GetTemperature();
  HandleFridgeControl();
  web_server.handleClient();
  ArduinoOTA.handle();
}
